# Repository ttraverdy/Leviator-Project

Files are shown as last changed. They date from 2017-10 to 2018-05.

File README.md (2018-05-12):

# What is the Leviator ?

The Leviator is a device made of two arrays of ultrasonic transducers, able to levitate and to control the movements of small objects such as styrofoam beads in 3 dimensions mid-air, using acoustic levitation. 

The levitation is possible thanks to standing wave created by the transducers of the device. Levitating objects are trapped in pressure nodes of those standing waves, surrounded by antinodes, which are going to apply forces on the object, making it levitate. The movements are made by modulating the phase of emission of the transducers. 

This project was awarded a first prize at the XXVth Olypimpiades de Physique, a national physics contest in France.

## How it works

The levitation is possible thanks to standing wave created by the transducers of the device. Levitating objects are trapped in pressure nodes of those standing waves, surrounded by antinodes, which are going to apply forces on the object, making it levitate. The movements are made by modulating the phase of emission of the transducers. 

To see our device work and to have a more precise explication of the movement method, click on the following image to watch a video of our Youtube channel :
<p align="center">
<a href="http://www.youtube.com/watch?feature=player_embedded&v=FV5mTikOukU
" target="_blank">The Leviator, levitation and control of movements using ultrsound</a>
</p>

## Want to build a Leviator ?

The 3D parts are available on this page in the STL folder. Many electronic parts are also necessary (list to be provided soon).

Assemble all the parts (Full instructions should soon be available on Instructables). The Fritzing schematic is available in the SCHEMA folder. It will show you the electronic schematic of the Leviator device.

Run the python 'generateMegaCode16x16new.py' program. This will generate a 'moveArray16x16.io' file in the 'generated' folder. Compile using your Arduino IDE and flash on the Arduino MEGA card.

## Future improvements

<p align="center">
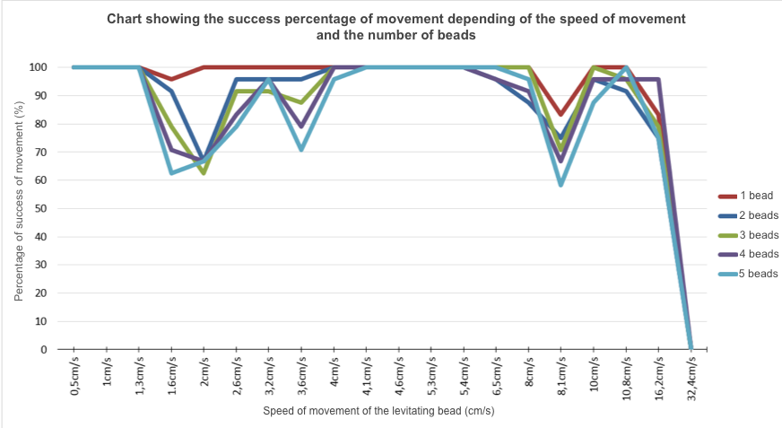
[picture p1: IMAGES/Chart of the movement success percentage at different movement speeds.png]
   
</p>
The actual maximum reliable movement speed is 10.5cm per second for 1 to 5 beads. 100% success rate movement speeds are 0.5cm to 1.5cm/s speeds and speeds from 4.1 to 5.4 cm per second. If more beads are put in a node, the success rate decreases.

We are planning to make a new Leviator, smaller and modular. 3D pieces of the protoype are available in the STL folder. Here is a photo of the actual prototype of the new Leviator. 
<p align="center">
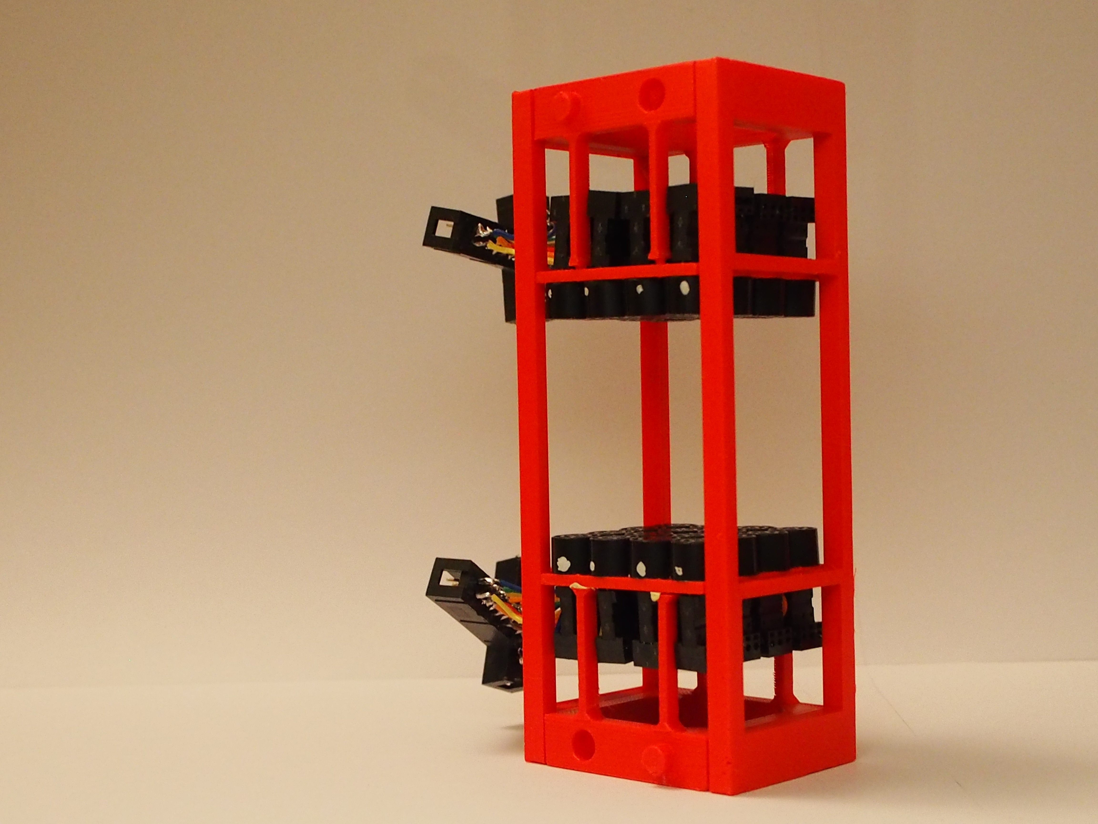
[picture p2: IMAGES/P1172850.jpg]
  
<p align="center">

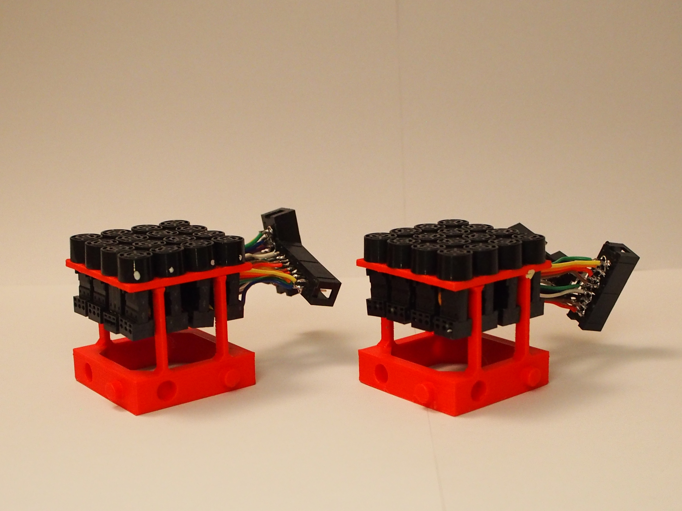
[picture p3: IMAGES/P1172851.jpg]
   
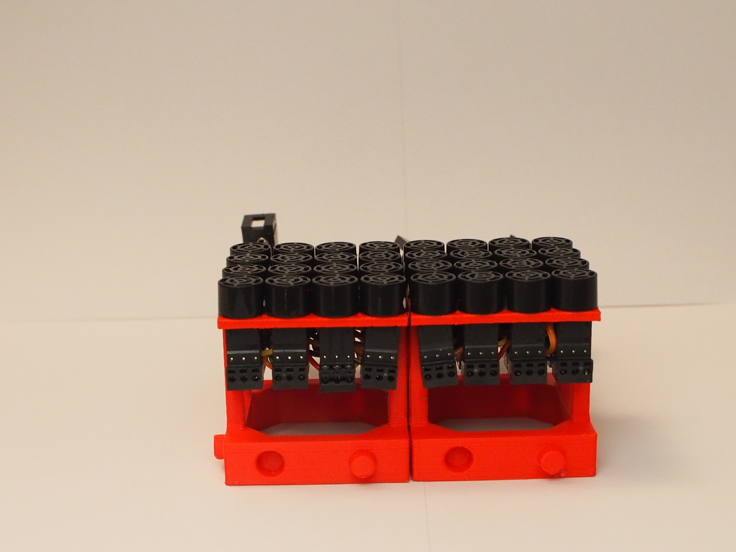
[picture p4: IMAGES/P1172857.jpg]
   
</p>
The new version will be smaller using 10mm diameter transducers and will be modular. Multiple Leviators will be able to be chained to increase the space in which beads will be able to be moved into.

We successfully made a first prototype of the transducer part of the Leviator. We are now working on the miniaturization of power supply of the device. We are actually testing different prototypes such as L293D or TC4427A MOSFET. 
We made different PCB circuits using CNC milling machines or by chemical way using iron perchloride.

## Credits and similar projects

Many thanks to Professor [Takayuki Hoshi](http://hoshistar81.jp/) from the University of Tokyo [Pixie Dust Technologies](http://pixiedusttech.com/) and to Mr. [Asier Marzo](https://www.researchgate.net/profile/Asier_Marzo) from the Bristol University [BigLev/TinyLev and Acoustic Tractor Beam projects](http://www.instructables.com/member/Asier%20Marzo/)

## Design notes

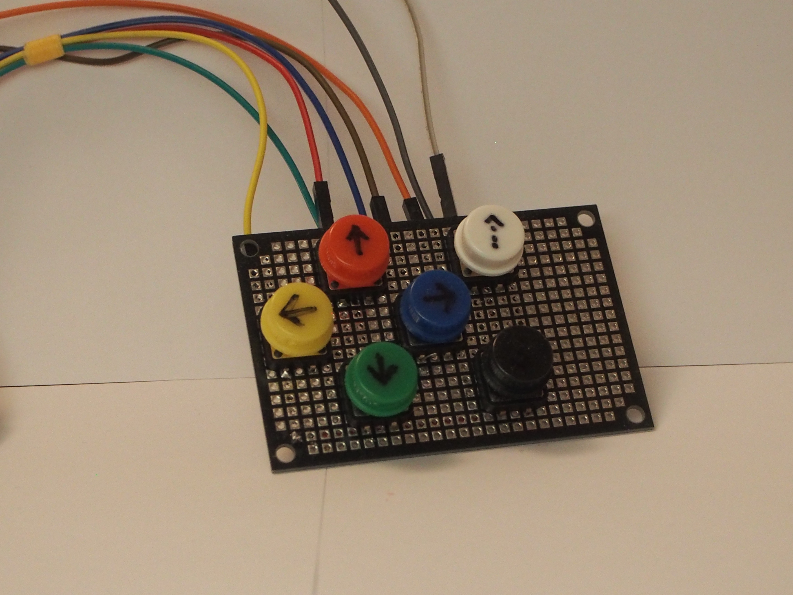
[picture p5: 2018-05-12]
IMAGES/The Leviator button pad.jpg

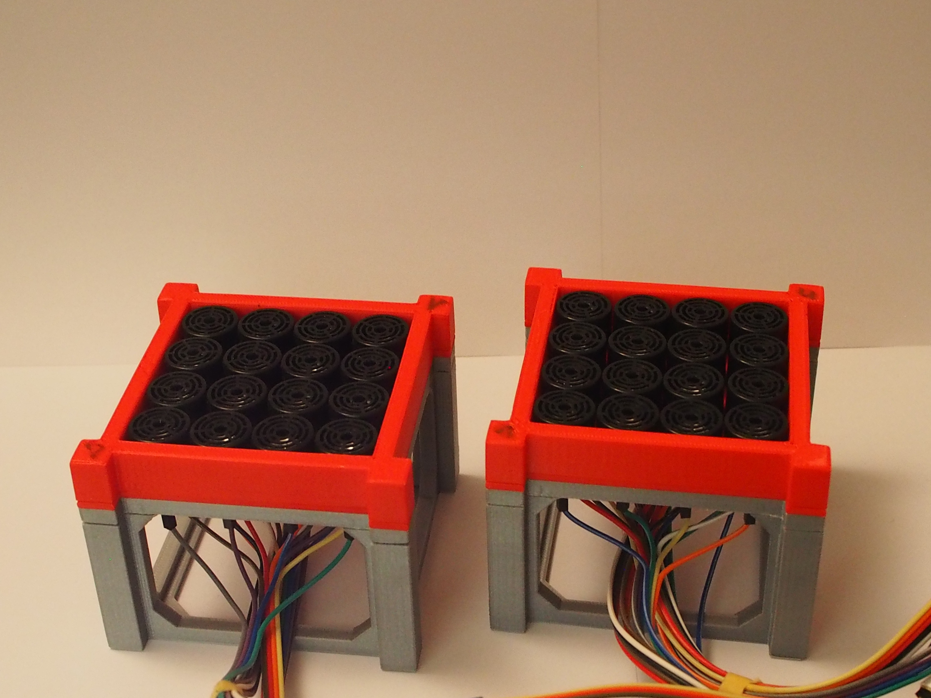
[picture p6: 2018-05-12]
IMAGES/The arrays of the Leviator (1).jpg

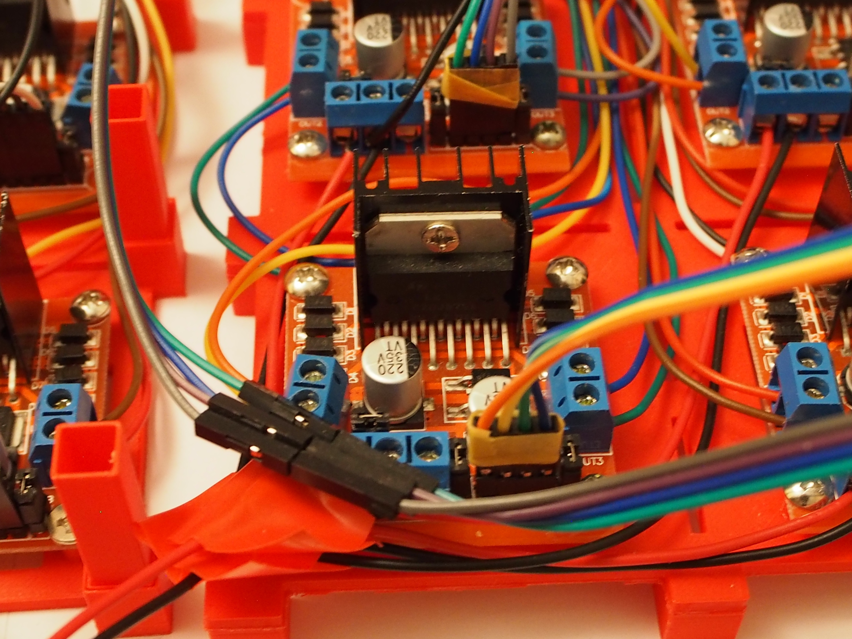
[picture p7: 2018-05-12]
IMAGES/L298N driver block (2).jpg

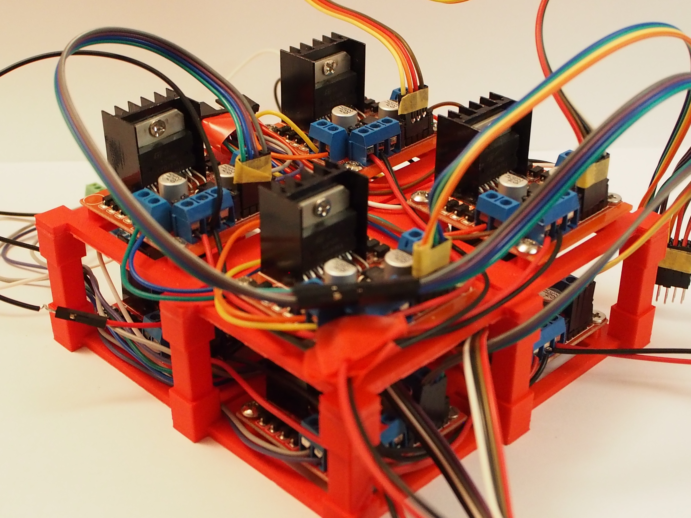
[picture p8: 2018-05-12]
IMAGES/L298N driver block (3).jpg

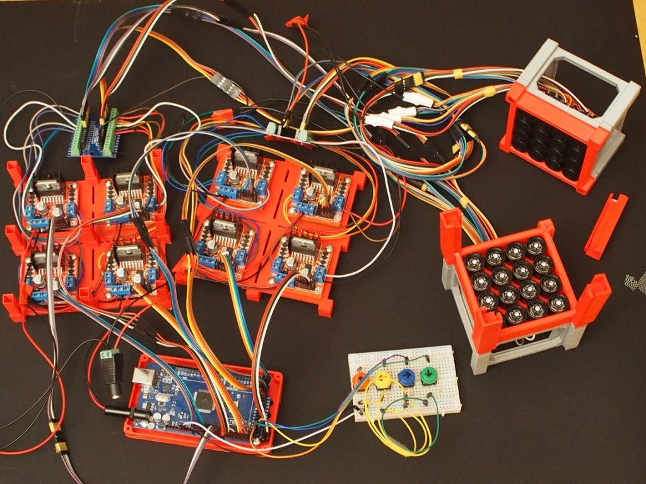
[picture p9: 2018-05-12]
IMAGES/The whole circuit.jpg

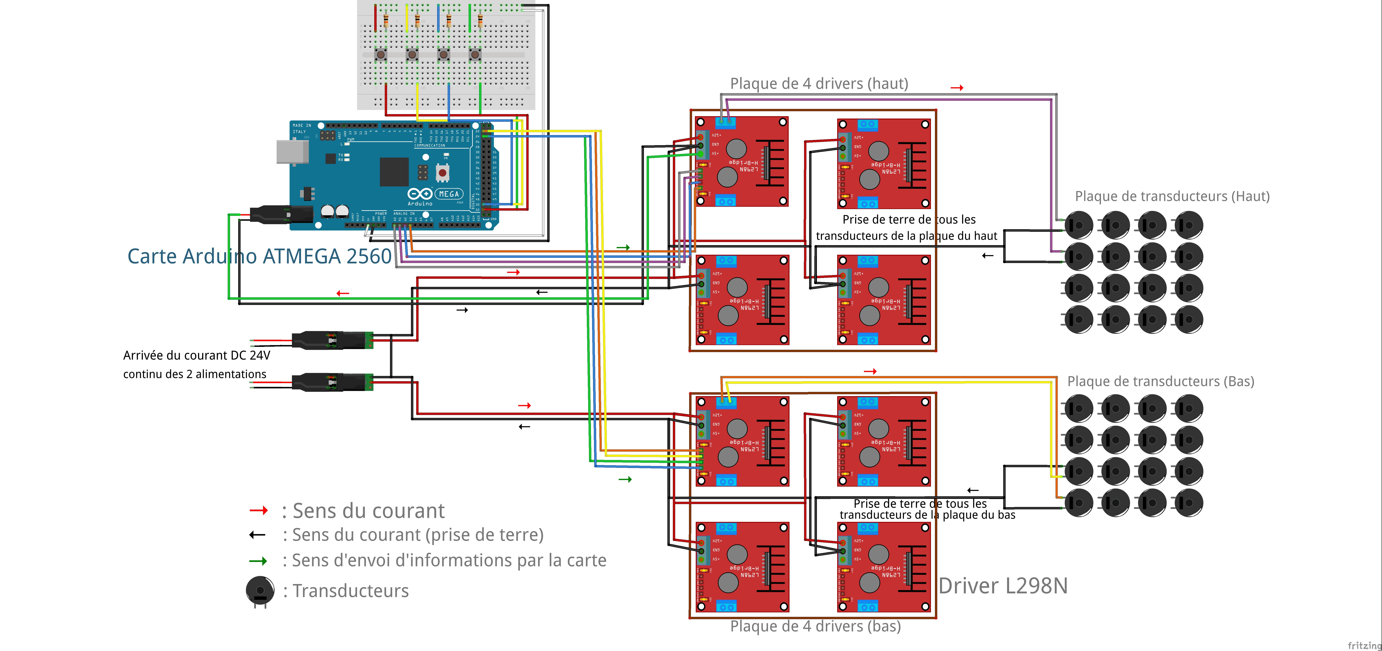
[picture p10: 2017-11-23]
SCHEMA/Schéma Léviator_bb.jpg

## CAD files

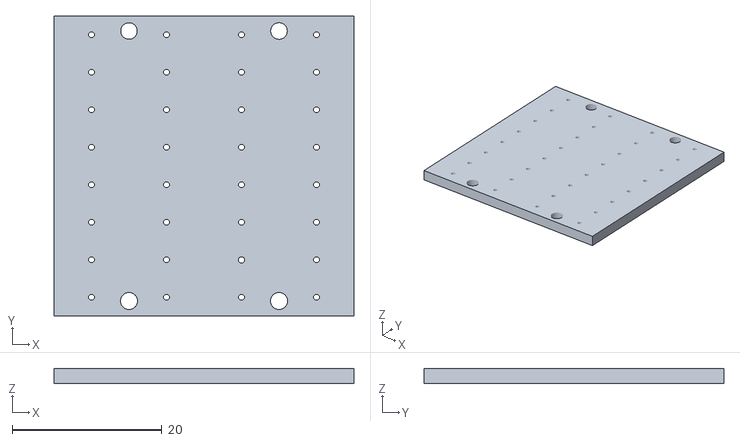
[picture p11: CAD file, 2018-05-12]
STL/Leviator 2 prototype part 2.stl
40.0 x 40.0 x 2.00

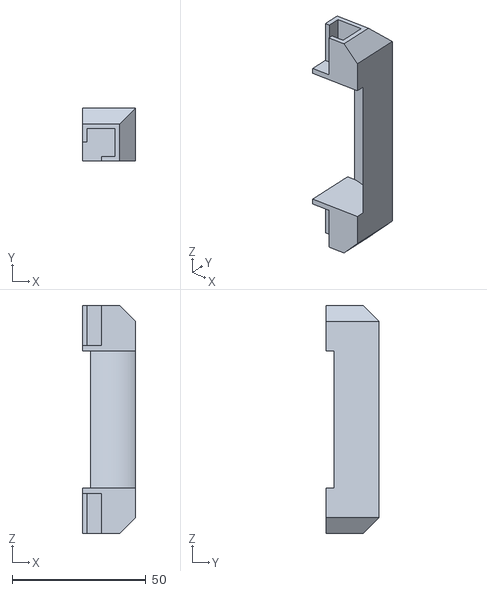
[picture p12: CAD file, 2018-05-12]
STL/Pilar of the Leviator n°3.stl
20.0 x 20.0 x 85.2

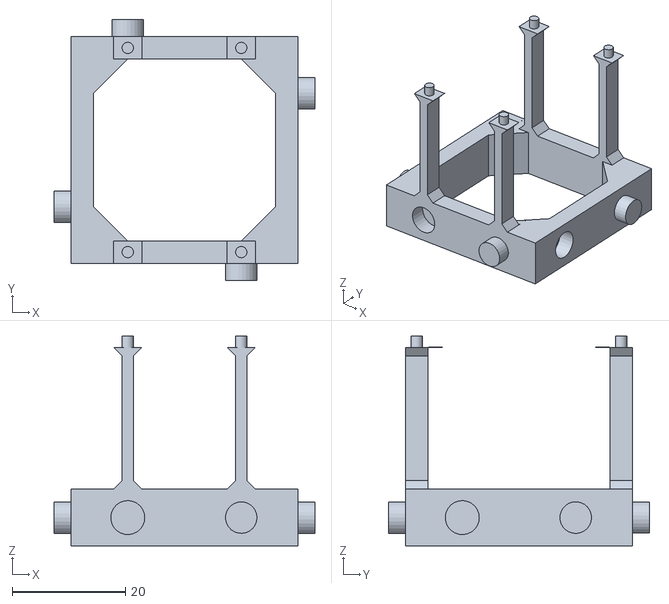
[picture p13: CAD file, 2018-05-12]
STL/Leviator 2 Prototype part 1.stl
46.0 x 46.0 x 37.0

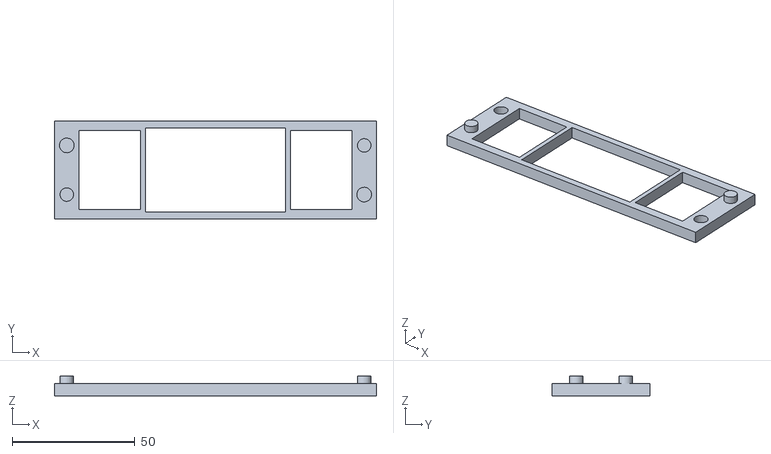
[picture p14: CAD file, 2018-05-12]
STL/Leviator prototype part 3.stl
131.0 x 40.0 x 8.00

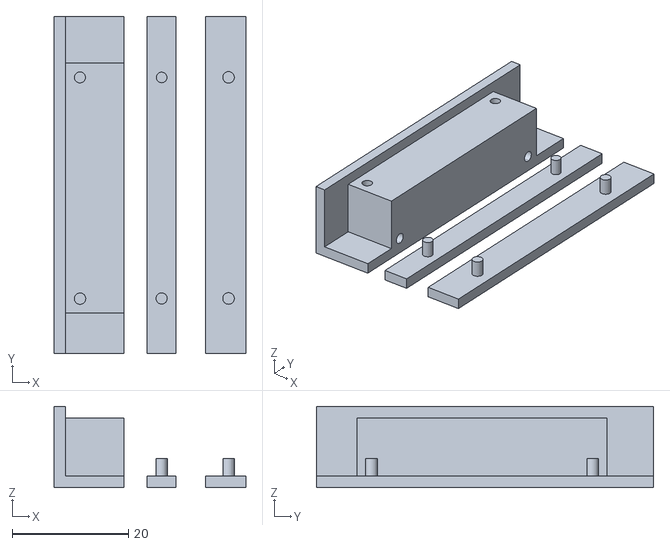
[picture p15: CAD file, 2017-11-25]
STL/Pilar of the Leviator n°2.stl
33.0 x 58.0 x 14.0

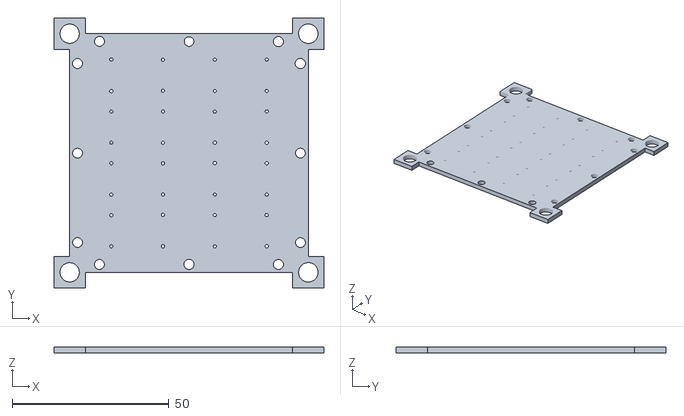
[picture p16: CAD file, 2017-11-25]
STL/Part 3 of the Leviator.stl
86.0 x 86.0 x 2.00

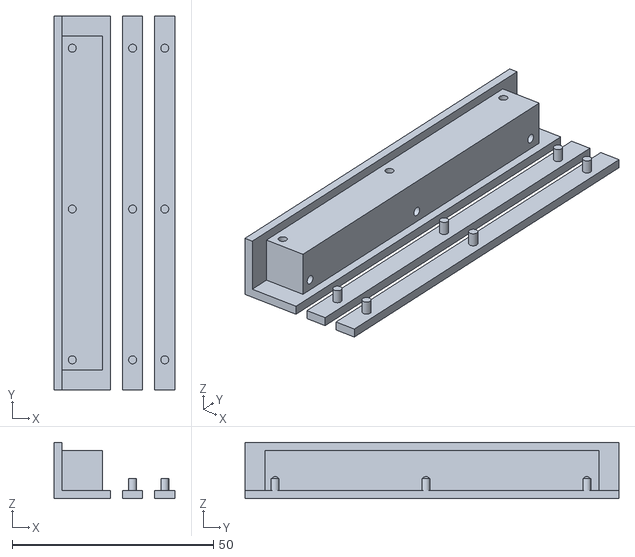
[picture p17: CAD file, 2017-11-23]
STL/Pilar of the Leviator n°1.stl
30.0 x 93.0 x 14.0

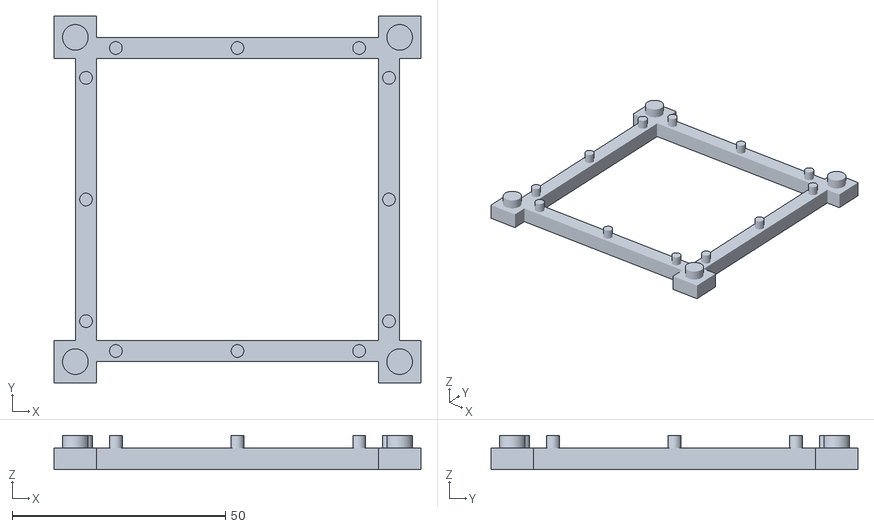
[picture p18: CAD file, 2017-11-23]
STL/Part 2 of the Leviator.stl
86.0 x 86.0 x 8.00

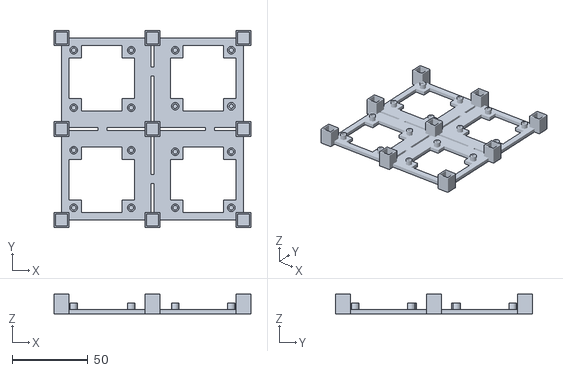
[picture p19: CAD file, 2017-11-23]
STL/Support for L298N drivers bottom.stl
130.0 x 130.0 x 13.0

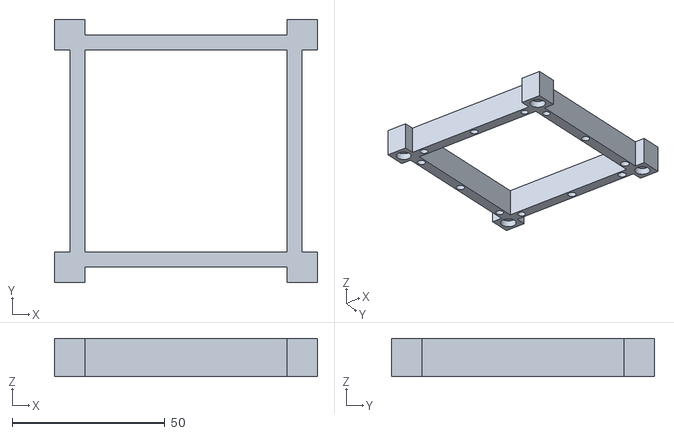
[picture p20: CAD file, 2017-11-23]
STL/Part 4 of the Leviator.stl
86.0 x 86.0 x 12.5

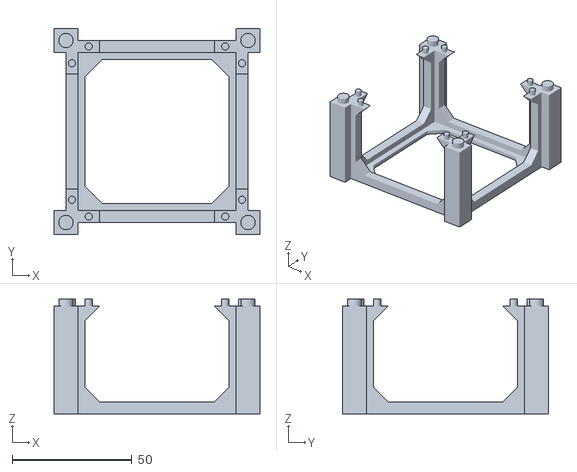
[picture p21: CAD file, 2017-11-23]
STL/Part 1 of the Leviator.stl
86.0 x 86.0 x 48.0

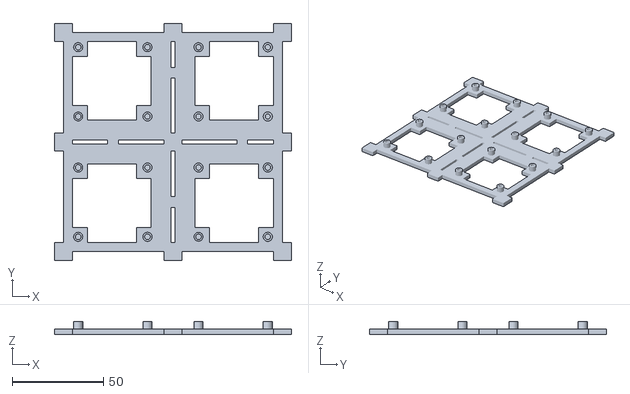
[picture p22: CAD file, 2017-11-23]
STL/Support for 4 L298N drivers top.stl
130.0 x 130.0 x 7.00

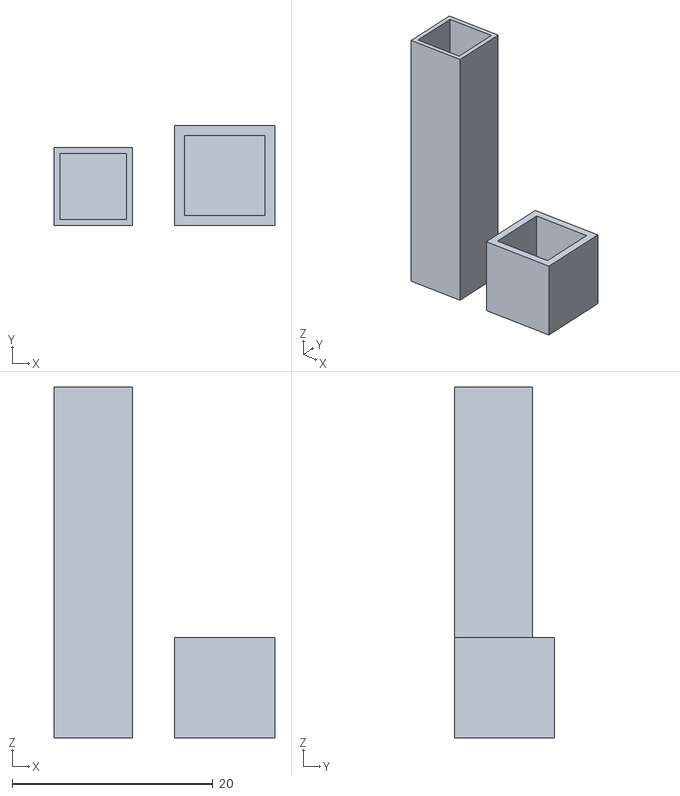
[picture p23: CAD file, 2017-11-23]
STL/Pilar for the support of L298N drivers.stl
22.0 x 10.0 x 35.0

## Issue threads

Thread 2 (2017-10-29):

add button support

ttraverdy, 2017-10-29:
- [x] button input
- [x] test on off

pgraverdy, 2017-11-02:
- cannot use digitalread, too slow for 40khz
- cannot use input_pullup (internal resistor too weak) too many false positive
- with 10komh resistor still some false positive
- added buttonreleased bool to wait for button release before doing the anim again (issue with some false positive from time to time)

Closed 2017-11-02.

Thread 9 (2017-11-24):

Documentation

pgraverdy, 2017-11-24:
- [ ] mettre a jour les noms des fichiers STL (en)
- [ ] mettre le fichier fritzing
- [ ] mettre a jour le readme avec images, ligne de commande
- [ ] mettre a jour le no du prg python, effacer les anciens plus utilisés
- [ ] commenter le code
- [ ] commenter la sortie arduino dans le doc
- [ ] mettre photos du montage complet monté et demonté
- [ ] mettre liste des composants et liens vers sites marchands
- [ ] mettre schema / table de connexion pour les cables sur l'arduino

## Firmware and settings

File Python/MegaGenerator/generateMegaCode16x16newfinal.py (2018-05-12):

#
# This code defines
#
#
#


# defines constants for generating the code for 2 4x4 transducer arrays

# defines the mapping between the port used on the arduino mega and the transducer
# each transducer is indentified with the triplet (s, x, y) with s being the side, and x, y being the position on the array
# two transducers on opposing arrays and with the same x,y are facing each other.
# side can be 0 or 1 (we consider only 2 opposiing array
sides = 2
sizeArray = 4

# number of ports used
nbPortsUsed = 32

# defines the number of frames/steps for each loop.
# this depends of the number of ports used and the time it takes to iterate, still maintiaining the 40Khz freq
# for the initial code (arduino uno, 4 ports it is 24 frames but for many ports, 12 frames should be used
#
MAX_FRAMES = 12
MAX_PORTS = 4

transducersPorts = ['PORTF', 'PORTF', 'PORTF', 'PORTF', 'PORTF', 'PORTF', 'PORTF', 'PORTF',
                    'PORTK', 'PORTK', 'PORTK', 'PORTK', 'PORTK', 'PORTK', 'PORTK', 'PORTK',
                    'PORTA', 'PORTA', 'PORTA', 'PORTA', 'PORTA', 'PORTA', 'PORTA', 'PORTA',
                    'PORTC', 'PORTC', 'PORTC', 'PORTC', 'PORTC', 'PORTC', 'PORTC', 'PORTC']

transducersBitmask = ['00000001', '00000010', '00000100', '00001000', '00010000', '00100000', '01000000', '10000000',
                      '00000001', '00000010', '00000100', '00001000', '00010000', '00100000', '01000000', '10000000',
                      '00000001', '00000010', '00000100', '00001000', '00010000', '00100000', '01000000', '10000000',
                      '10000000', '01000000', '00100000', '00010000', '00001000', '00000100', '00000010', '00000001']

arduinoPorts = ['PORTF', 'PORTK', 'PORTA', 'PORTC']
arduinoPortValues = {}

# we consider that transducers can be at the following state
# 0 - off
# 1 - is the transducer that has the particle
# 2 - is a transducer around the one that has the particule
STATE_TRANSDUCER_OFF = 0
STATE_TRANSDUCER_NB = 1
STATE_TRANSDUCER_PART = 2

transducerFramesOff = [0x00, 0x00, 0x00, 0x00, 0x00, 0x00, 0x00, 0x00, 0x00, 0x00, 0x00, 0x00]
transducerFramesNeighbor2 = [0xff, 0xff, 0xff, 0xff, 0xff, 0xff, 0x00, 0x00, 0x00, 0x00, 0x00, 0x00]
transducerFramesNeighbor3 = [0x00, 0x00, 0x00, 0x00, 0x00, 0x00, 0x00, 0x00, 0x00, 0x00, 0x00, 0x00]
transducerFramesParticle = [0x00, 0x00, 0x00, 0x00, 0x00, 0x00, 0xff, 0xff, 0xff, 0xff, 0xff, 0xff]
transducerFramesNeighbor = [0x00, 0x00, 0x00, 0x00, 0x00, 0x00, 0x00, 0x00, 0x00, 0x00, 0x00, 0x00]

MAX_ANIM_STEPS = 12

STATE_TRANSDUCER_NB2NB = 1
STATE_TRANSDUCER_NB2OFF = 2
STATE_TRANSDUCER_OFF2NB = 3
STATE_TRANSDUCER_OFF2OFF = 4
STATE_TRANSDUCER_NB2PART = 5
STATE_TRANSDUCER_PART2NB = 6
STATE_TRANSDUCER_PART2PART = 7

##
## definitions for animations - various combinations - one is selected after
##

##
## for 10mm transducers
##
# The next tables defines in hexadecimal the action of each postion in object's movement for a Leviator using 10mm transducers

transducerAnimationParticleToParticle10mm = [
# This one defines the evolution of the phase of the 2 transduceurs of the middle of the 6 transducers used in one move
#    [0x00, 0x00, 0x00, 0x00, 0x00, 0x00, 0xff, 0xff, 0xff, 0xff, 0xff, 0xff],
    [0x00, 0x00, 0x00, 0x00, 0x00, 0x00, 0xff, 0xff, 0xff, 0xff, 0xff, 0xff],
    [0x00, 0x00, 0x00, 0x00, 0x00, 0x00, 0xff, 0xff, 0xff, 0xff, 0xff, 0xff],
    [0x00, 0x00, 0x00, 0x00, 0x00, 0xff, 0xff, 0xff, 0xff, 0xff, 0xff, 0x00],
    [0x00, 0x00, 0x00, 0x00, 0x00, 0xff, 0xff, 0xff, 0xff, 0xff, 0xff, 0x00],
    [0x00, 0x00, 0x00, 0x00, 0x00, 0xff, 0xff, 0xff, 0xff, 0xff, 0xff, 0x00],
    [0x00, 0x00, 0x00, 0x00, 0x00, 0xff, 0xff, 0xff, 0xff, 0xff, 0xff, 0x00],
    [0x00, 0x00, 0x00, 0x00, 0x00, 0xff, 0xff, 0xff, 0xff, 0xff, 0xff, 0x00],
    [0x00, 0x00, 0x00, 0x00, 0x00, 0xff, 0xff, 0xff, 0xff, 0xff, 0xff, 0x00],
    [0x00, 0x00, 0x00, 0x00, 0x00, 0xff, 0xff, 0xff, 0xff, 0xff, 0xff, 0x00],
    [0x00, 0x00, 0x00, 0x00, 0x00, 0x00, 0xff, 0xff, 0xff, 0xff, 0xff, 0xff],
    [0x00, 0x00, 0x00, 0x00, 0x00, 0x00, 0xff, 0xff, 0xff, 0xff, 0xff, 0xff],
    [0x00, 0x00, 0x00, 0x00, 0x00, 0x00, 0xff, 0xff, 0xff, 0xff, 0xff, 0xff]
]


transducerAnimationParticleToNeighbor10mm = [
# This one defines the evolution of the phase of the 2 transduceurs of the old postion of the 6 transducers used in one move

#    [0xff, 0xff, 0xff, 0xff, 0xff, 0x00, 0x00, 0x00, 0x00, 0x00, 0x00, 0xff]
    [0xff, 0xff, 0xff, 0xff, 0xff, 0x00, 0x00, 0x00, 0x00, 0x00, 0x00, 0xff],
    [0xff, 0xff, 0xff, 0xff, 0x00, 0x00, 0x00, 0x00, 0x00, 0x00, 0xff, 0xff],
    [0xff, 0xff, 0xff, 0x00, 0x00, 0x00, 0x00, 0x00, 0x00, 0xff, 0xff, 0xff],
    [0xff, 0xff, 0xff, 0x00, 0x00, 0x00, 0x00, 0x00, 0x00, 0xff, 0xff, 0xff],
    [0xff, 0xff, 0x00, 0x00, 0x00, 0x00, 0x00, 0x00, 0xff, 0xff, 0xff, 0xff],
    [0xff, 0xff, 0x00, 0x00, 0x00, 0x00, 0x00, 0x00, 0xff, 0xff, 0xff, 0xff],
    [0xff, 0xff, 0x00, 0x00, 0x00, 0x00, 0x00, 0x00, 0xff, 0xff, 0xff, 0xff],
    [0xff, 0x00, 0x00, 0x00, 0x00, 0x00, 0x00, 0xff, 0xff, 0xff, 0xff, 0xff],
    [0xff, 0x00, 0x00, 0x00, 0x00, 0x00, 0x00, 0xff, 0xff, 0xff, 0xff, 0xff],
    [0xff, 0x00, 0x00, 0x00, 0x00, 0x00, 0x00, 0xff, 0xff, 0xff, 0xff, 0xff],
    [0x00, 0x00, 0x00, 0x00, 0x00, 0x00, 0xff, 0xff, 0xff, 0xff, 0xff, 0xff],
    [0x00, 0x00, 0x00, 0x00, 0x00, 0x00, 0xff, 0xff, 0xff, 0xff, 0xff, 0xff]
]

transducerAnimationNeighborToParticle10mm = [
# This one defines the evolution of the phase of the 2 transduceurs of the new postion of the 6 transducers used in one move

#    [0x00, 0x00, 0x00, 0x00, 0x00, 0x00, 0xff, 0xff, 0xff, 0xff, 0xff, 0xff]
    [0x00, 0x00, 0x00, 0x00, 0x00, 0x00, 0xff, 0xff, 0xff, 0xff, 0xff, 0xff],
    [0xff, 0x00, 0x00, 0x00, 0x00, 0x00, 0x00, 0xff, 0xff, 0xff, 0xff, 0xff],
    [0xff, 0x00, 0x00, 0x00, 0x00, 0x00, 0x00, 0xff, 0xff, 0xff, 0xff, 0xff],
    [0xff, 0x00, 0x00, 0x00, 0x00, 0x00, 0x00, 0xff, 0xff, 0xff, 0xff, 0xff],
    [0xff, 0xff, 0x00, 0x00, 0x00, 0x00, 0x00, 0x00, 0xff, 0xff, 0xff, 0xff],
    [0xff, 0xff, 0x00, 0x00, 0x00, 0x00, 0x00, 0x00, 0xff, 0xff, 0xff, 0xff],
    [0xff, 0xff, 0x00, 0x00, 0x00, 0x00, 0x00, 0x00, 0xff, 0xff, 0xff, 0xff],
    [0xff, 0xff, 0xff, 0x00, 0x00, 0x00, 0x00, 0x00, 0x00, 0xff, 0xff, 0xff],
    [0xff, 0xff, 0xff, 0x00, 0x00, 0x00, 0x00, 0x00, 0x00, 0xff, 0xff, 0xff],
    [0xff, 0xff, 0xff, 0xff, 0x00, 0x00, 0x00, 0x00, 0x00, 0x00, 0xff, 0xff],
    [0xff, 0xff, 0xff, 0xff, 0xff, 0x00, 0x00, 0x00, 0x00, 0x00, 0x00, 0xff],
    [0xff, 0xff, 0xff, 0xff, 0xff, 0x00, 0x00, 0x00, 0x00, 0x00, 0x00, 0xff]
]

## 16mm - phase 32mm

transducerAnimationParticleToParticle16mm = [
# This one defines the evolution of the phase of the 2 transduceurs of the middle of the 6 transducers used in one move

    [0x00, 0x00, 0x00, 0x00, 0x00, 0x00, 0xff, 0xff, 0xff, 0xff, 0xff, 0xff],
    [0x00, 0x00, 0x00, 0x00, 0x00, 0x00, 0xff, 0xff, 0xff, 0xff, 0xff, 0xff],
    [0x00, 0x00, 0x00, 0x00, 0x00, 0xff, 0xff, 0xff, 0xff, 0xff, 0xff, 0x00],
    [0x00, 0x00, 0x00, 0x00, 0x00, 0xff, 0xff, 0xff, 0xff, 0xff, 0xff, 0x00],
    [0x00, 0x00, 0x00, 0x00, 0x00, 0xff, 0xff, 0xff, 0xff, 0xff, 0xff, 0x00],
    [0x00, 0x00, 0x00, 0x00, 0x00, 0xff, 0xff, 0xff, 0xff, 0xff, 0xff, 0x00],
#    [0x00, 0x00, 0x00, 0x00, 0x00, 0xff, 0xff, 0xff, 0xff, 0xff, 0xff, 0x00],
    [0x00, 0x00, 0x00, 0x00, 0x00, 0xff, 0xff, 0xff, 0xff, 0xff, 0xff, 0x00],
    [0x00, 0x00, 0x00, 0x00, 0x00, 0xff, 0xff, 0xff, 0xff, 0xff, 0xff, 0x00],
    [0x00, 0x00, 0x00, 0x00, 0x00, 0xff, 0xff, 0xff, 0xff, 0xff, 0xff, 0x00],
    [0x00, 0x00, 0x00, 0x00, 0x00, 0xff, 0xff, 0xff, 0xff, 0xff, 0xff, 0x00],
    [0x00, 0x00, 0x00, 0x00, 0x00, 0x00, 0xff, 0xff, 0xff, 0xff, 0xff, 0xff],
    [0x00, 0x00, 0x00, 0x00, 0x00, 0x00, 0xff, 0xff, 0xff, 0xff, 0xff, 0xff]
]

transducerAnimationParticleToNeighbor16mm = [
# This one defines the evolution of the phase of the 2 transduceurs of the old postion of the 6 transducers used in one move

    [0x00, 0x00, 0x00, 0x00, 0xff, 0xff, 0xff, 0xff, 0xff, 0xff, 0x00, 0x00],
    [0x00, 0x00, 0x00, 0xff, 0xff, 0xff, 0xff, 0xff, 0xff, 0x00, 0x00, 0x00],
    [0x00, 0x00, 0xff, 0xff, 0xff, 0xff, 0xff, 0xff, 0x00, 0x00, 0x00, 0x00],
    [0x00, 0xff, 0xff, 0xff, 0xff, 0xff, 0xff, 0x00, 0x00, 0x00, 0x00, 0x00],
    [0xff, 0xff, 0xff, 0xff, 0xff, 0xff, 0x00, 0x00, 0x00, 0x00, 0x00, 0x00],
    [0xff, 0xff, 0xff, 0xff, 0xff, 0x00, 0x00, 0x00, 0x00, 0x00, 0x00, 0xff],
#    [0xff, 0xff, 0xff, 0xff, 0x00, 0x00, 0x00, 0x00, 0x00, 0x00, 0xff, 0xff],
    [0xff, 0xff, 0xff, 0x00, 0x00, 0x00, 0x00, 0x00, 0x00, 0xff, 0xff, 0xff],
    [0xff, 0xff, 0x00, 0x00, 0x00, 0x00, 0x00, 0x00, 0xff, 0xff, 0xff, 0xff],
    [0xff, 0xff, 0x00, 0x00, 0x00, 0x00, 0x00, 0x00, 0xff, 0xff, 0xff, 0xff],
    [0xff, 0x00, 0x00, 0x00, 0x00, 0x00, 0x00, 0xff, 0xff, 0xff, 0xff, 0xff],
    [0xff, 0x00, 0x00, 0x00, 0x00, 0x00, 0x00, 0xff, 0xff, 0xff, 0xff, 0xff],
    [0x00, 0x00, 0x00, 0x00, 0x00, 0x00, 0xff, 0xff, 0xff, 0xff, 0xff, 0xff]
]
transducerAnimationNeighborToParticle16mm = [
# This one defines the evolution of the phase of the 2 transduceurs of the new postion of the 6 transducers used in one move

    [0x00, 0x00, 0x00, 0x00, 0x00, 0x00, 0xff, 0xff, 0xff, 0xff, 0xff, 0xff],
    [0xff, 0x00, 0x00, 0x00, 0x00, 0x00, 0x00, 0xff, 0xff, 0xff, 0xff, 0xff],
    [0xff, 0x00, 0x00, 0x00, 0x00, 0x00, 0x00, 0xff, 0xff, 0xff, 0xff, 0xff],
    [0xff, 0xff, 0x00, 0x00, 0x00, 0x00, 0x00, 0x00, 0xff, 0xff, 0xff, 0xff],
    [0xff, 0xff, 0x00, 0x00, 0x00, 0x00, 0x00, 0x00, 0xff, 0xff, 0xff, 0xff],
    [0xff, 0xff, 0xff, 0x00, 0x00, 0x00, 0x00, 0x00, 0x00, 0xff, 0xff, 0xff],
#    [0xff, 0xff, 0xff, 0xff, 0x00, 0x00, 0x00, 0x00, 0x00, 0x00, 0xff, 0xff],
    [0xff, 0xff, 0xff, 0xff, 0xff, 0x00, 0x00, 0x00, 0x00, 0x00, 0x00, 0xff],
    [0xff, 0xff, 0xff, 0xff, 0xff, 0xff, 0x00, 0x00, 0x00, 0x00, 0x00, 0x00],
    [0x00, 0xff, 0xff, 0xff, 0xff, 0xff, 0xff, 0x00, 0x00, 0x00, 0x00, 0x00],
    [0x00, 0x00, 0xff, 0xff, 0xff, 0xff, 0xff, 0xff, 0x00, 0x00, 0x00, 0x00],
    [0x00, 0x00, 0x00, 0xff, 0xff, 0xff, 0xff, 0xff, 0xff, 0x00, 0x00, 0x00],
    [0x00, 0x00, 0x00, 0x00, 0xff, 0xff, 0xff, 0xff, 0xff, 0xff, 0x00, 0x00]
]


##
## Amplitude
##

#different tables of hexadecimal values for transducers activation for movement using the amplitude modulation method, which isn't very trustworthy

transducerAnimationParticleToNeighborGOOD = [
    [0x00, 0x00, 0x00, 0x00, 0x00, 0x00, 0x00, 0x00, 0xff, 0xff, 0x00, 0x00],
    [0x00, 0x00, 0x00, 0x00, 0x00, 0x00, 0x00, 0x00, 0x00, 0xff, 0x00, 0x00],
    [0x00, 0x00, 0x00, 0x00, 0x00, 0x00, 0x00, 0x00, 0x00, 0xff, 0x00, 0x00],
    [0x00, 0x00, 0x00, 0x00, 0x00, 0x00, 0x00, 0x00, 0x00, 0x00, 0x00, 0x00],
    [0x00, 0x00, 0x00, 0x00, 0x00, 0x00, 0x00, 0x00, 0x00, 0x00, 0x00, 0x00],
    [0x00, 0x00, 0xff, 0x00, 0x00, 0x00, 0x00, 0x00, 0x00, 0x00, 0x00, 0x00],
    [0x00, 0x00, 0xff, 0x00, 0x00, 0x00, 0x00, 0x00, 0x00, 0x00, 0x00, 0x00],
    [0x00, 0xff, 0xff, 0xff, 0x00, 0x00, 0x00, 0x00, 0x00, 0x00, 0x00, 0x00],
    [0x00, 0x00, 0xff, 0x00, 0x00, 0x00, 0x00, 0x00, 0x00, 0x00, 0x00, 0x00],
    [0x00, 0x00, 0xff, 0x00, 0x00, 0x00, 0x00, 0x00, 0x00, 0x00, 0x00, 0x00],
    [0x00, 0x00, 0x00, 0x00, 0x00, 0x00, 0x00, 0x00, 0x00, 0x00, 0x00, 0x00],
    [0x00, 0x00, 0x00, 0x00, 0x00, 0x00, 0x00, 0x00, 0x00, 0x00, 0x00, 0x00],
    [0x00, 0x00, 0x00, 0x00, 0x00, 0x00, 0x00, 0x00, 0x00, 0x00, 0x00, 0x00],
    [0x00, 0x00, 0x00, 0x00, 0x00, 0x00, 0x00, 0x00, 0x00, 0x00, 0x00, 0x00],
    [0x00, 0x00, 0x00, 0x00, 0x00, 0x00, 0x00, 0x00, 0x00, 0x00, 0x00, 0x00],
    [0x00, 0x00, 0x00, 0x00, 0x00, 0x00, 0x00, 0x00, 0x00, 0x00, 0x00, 0x00]
]

transducerAnimationParticleToParticleGOOD = [
    [0x00, 0x00, 0x00, 0x00, 0x00, 0x00, 0xff, 0xff, 0xff, 0xff, 0xff, 0xff],
    [0x00, 0x00, 0x00, 0x00, 0x00, 0x00, 0xff, 0xff, 0xff, 0xff, 0xff, 0xff],
    [0x00, 0x00, 0x00, 0x00, 0x00, 0x00, 0xff, 0xff, 0xff, 0xff, 0xff, 0xff],
    [0x00, 0x00, 0x00, 0x00, 0x00, 0x00, 0xff, 0xff, 0xff, 0xff, 0xff, 0xff],
    [0x00, 0x00, 0x00, 0x00, 0x00, 0x00, 0xff, 0xff, 0xff, 0xff, 0xff, 0xff],
    [0x00, 0x00, 0x00, 0x00, 0x00, 0x00, 0xff, 0xff, 0xff, 0xff, 0xff, 0xff],
    [0x00, 0x00, 0x00, 0x00, 0x00, 0x00, 0x00, 0xff, 0xff, 0xff, 0xff, 0x00],
    [0x00, 0x00, 0x00, 0x00, 0x00, 0x00, 0x00, 0xff, 0xff, 0xff, 0xff, 0x00],
    [0x00, 0x00, 0x00, 0x00, 0x00, 0x00, 0x00, 0x00, 0xff, 0xff, 0x00, 0x00],
    [0x00, 0x00, 0x00, 0x00, 0x00, 0x00, 0x00, 0x00, 0xff, 0xff, 0x00, 0x00],
    [0x00, 0x00, 0x00, 0x00, 0x00, 0x00, 0x00, 0x00, 0x00, 0xff, 0x00, 0x00],
    [0x00, 0x00, 0x00, 0x00, 0x00, 0x00, 0x00, 0x00, 0xff, 0xff, 0x00, 0x00],
    [0x00, 0x00, 0x00, 0x00, 0x00, 0x00, 0x00, 0xff, 0xff, 0xff, 0xff, 0x00],
    [0x00, 0x00, 0x00, 0x00, 0x00, 0x00, 0x00, 0xff, 0xff, 0xff, 0xff, 0x00],
    [0x00, 0x00, 0x00, 0x00, 0x00, 0x00, 0xff, 0xff, 0xff, 0xff, 0xff, 0xff],
    [0x00, 0x00, 0x00, 0x00, 0x00, 0x00, 0xff, 0xff, 0xff, 0xff, 0xff, 0xff]
]

# better than transducerAnimationNeighborToParticle4
transducerAnimationNeighborToParticleGOOD = [
    [0x00, 0x00, 0x00, 0x00, 0x00, 0x00, 0x00, 0x00, 0x00, 0x00, 0x00, 0x00],
    [0x00, 0x00, 0x00, 0x00, 0x00, 0x00, 0x00, 0x00, 0x00, 0x00, 0x00, 0x00],
    [0x00, 0x00, 0x00, 0x00, 0x00, 0x00, 0x00, 0x00, 0x00, 0x00, 0x00, 0x00],
    [0x00, 0x00, 0x00, 0x00, 0x00, 0x00, 0x00, 0x00, 0x00, 0x00, 0x00, 0x00],
    [0x00, 0x00, 0x00, 0x00, 0x00, 0x00, 0x00, 0x00, 0x00, 0x00, 0x00, 0x00],
    [0x00, 0x00, 0x00, 0x00, 0x00, 0x00, 0x00, 0x00, 0x00, 0x00, 0x00, 0x00],
    [0x00, 0x00, 0x00, 0x00, 0x00, 0x00, 0x00, 0x00, 0x00, 0xff, 0x00, 0x00],
    [0x00, 0x00, 0x00, 0x00, 0x00, 0x00, 0x00, 0x00, 0xff, 0xff, 0x00, 0x00],
    [0x00, 0x00, 0x00, 0x00, 0x00, 0x00, 0x00, 0x00, 0xff, 0xff, 0x00, 0x00],
    [0x00, 0x00, 0x00, 0x00, 0x00, 0x00, 0x00, 0xff, 0xff, 0xff, 0x00, 0x00],
    [0x00, 0x00, 0x00, 0x00, 0x00, 0x00, 0x00, 0xff, 0xff, 0xff, 0xff, 0x00],
    [0x00, 0x00, 0x00, 0x00, 0x00, 0x00, 0x00, 0xff, 0xff, 0xff, 0xff, 0x00],
    [0x00, 0x00, 0x00, 0x00, 0x00, 0x00, 0xff, 0xff, 0xff, 0xff, 0xff, 0xff],
    [0x00, 0x00, 0x00, 0x00, 0x00, 0x00, 0xff, 0xff, 0xff, 0xff, 0xff, 0xff],
    [0x00, 0x00, 0x00, 0x00, 0x00, 0x00, 0xff, 0xff, 0xff, 0xff, 0xff, 0xff],
    [0x00, 0x00, 0x00, 0x00, 0x00, 0x00, 0xff, 0xff, 0xff, 0xff, 0xff, 0xff]
]
##
## Misc
##

#
transducerAnimationParticleToNeighbor4 = [
    [0x00, 0x00, 0x00, 0x00, 0x00, 0x00, 0x00, 0x00, 0xff, 0xff, 0x00, 0x00],
    [0x00, 0x00, 0x00, 0x00, 0x00, 0x00, 0x00, 0x00, 0x00, 0xff, 0x00, 0x00],
    [0x00, 0x00, 0x00, 0x00, 0x00, 0x00, 0x00, 0x00, 0x00, 0xff, 0x00, 0x00],
    [0x00, 0x00, 0x00, 0x00, 0x00, 0x00, 0x00, 0x00, 0x00, 0x00, 0x00, 0x00],
    [0x00, 0x00, 0x00, 0x00, 0x00, 0x00, 0x00, 0x00, 0x00, 0x00, 0x00, 0x00],
    [0x00, 0x00, 0xff, 0x00, 0x00, 0x00, 0x00, 0x00, 0x00, 0x00, 0x00, 0x00],
    [0x00, 0x00, 0xff, 0x00, 0x00, 0x00, 0x00, 0x00, 0x00, 0x00, 0x00, 0x00],
    [0x00, 0xff, 0xff, 0xff, 0x00, 0x00, 0x00, 0x00, 0x00, 0x00, 0x00, 0x00],
    [0x00, 0x00, 0xff, 0x00, 0x00, 0x00, 0x00, 0x00, 0x00, 0x00, 0x00, 0x00],
    [0x00, 0x00, 0xff, 0x00, 0x00, 0x00, 0x00, 0x00, 0x00, 0x00, 0x00, 0x00],
    [0x00, 0x00, 0x00, 0x00, 0x00, 0x00, 0x00, 0x00, 0x00, 0x00, 0x00, 0x00],
    [0x00, 0x00, 0x00, 0x00, 0x00, 0x00, 0x00, 0x00, 0x00, 0x00, 0x00, 0x00],
    [0x00, 0x00, 0x00, 0x00, 0x00, 0x00, 0x00, 0x00, 0x00, 0x00, 0x00, 0x00],
    [0x00, 0x00, 0x00, 0x00, 0x00, 0x00, 0x00, 0x00, 0x00, 0x00, 0x00, 0x00],
    [0x00, 0x00, 0x00, 0x00, 0x00, 0x00, 0x00, 0x00, 0x00, 0x00, 0x00, 0x00],
    [0x00, 0x00, 0x00, 0x00, 0x00, 0x00, 0x00, 0x00, 0x00, 0x00, 0x00, 0x00]
]

transducerAnimationParticleToNeighbor3 = [
    [0x00, 0x00, 0x00, 0x00, 0x00, 0x00, 0x00, 0xff, 0xff, 0xff, 0xff, 0x00],
    [0x00, 0x00, 0x00, 0x00, 0x00, 0x00, 0x00, 0xff, 0xff, 0xff, 0xff, 0x00],
    [0x00, 0x00, 0x00, 0x00, 0x00, 0x00, 0x00, 0x00, 0xff, 0xff, 0xff, 0x00],
    [0x00, 0x00, 0x00, 0x00, 0x00, 0x00, 0x00, 0x00, 0xff, 0xff, 0xff, 0x00],
    [0x00, 0x00, 0x00, 0x00, 0x00, 0x00, 0x00, 0x00, 0xff, 0xff, 0x00, 0x00],
    [0x00, 0x00, 0x00, 0x00, 0x00, 0x00, 0x00, 0x00, 0xff, 0xff, 0x00, 0x00],
    [0x00, 0x00, 0x00, 0x00, 0x00, 0x00, 0x00, 0x00, 0xff, 0xff, 0x00, 0x00],
    [0x00, 0x00, 0x00, 0x00, 0x00, 0x00, 0x00, 0x00, 0xff, 0xff, 0x00, 0x00],
    [0x00, 0x00, 0x00, 0xff, 0x00, 0x00, 0x00, 0x00, 0x00, 0x00, 0x00, 0x00],
    [0x00, 0x00, 0xff, 0xff, 0x00, 0x00, 0x00, 0x00, 0x00, 0x00, 0x00, 0x00],
    [0x00, 0x00, 0xff, 0xff, 0x00, 0x00, 0x00, 0x00, 0x00, 0x00, 0x00, 0x00],
    [0x00, 0x00, 0xff, 0xff, 0xff, 0x00, 0x00, 0x00, 0x00, 0x00, 0x00, 0x00],
    [0x00, 0xff, 0xff, 0xff, 0xff, 0x00, 0x00, 0x00, 0x00, 0x00, 0x00, 0x00],
    [0x00, 0xff, 0xff, 0xff, 0xff, 0xff, 0x00, 0x00, 0x00, 0x00, 0x00, 0x00],
    [0x00, 0xff, 0xff, 0xff, 0xff, 0xff, 0x00, 0x00, 0x00, 0x00, 0x00, 0x00],
    [0x00, 0xff, 0xff, 0xff, 0xff, 0xff, 0x00, 0x00, 0x00, 0x00, 0x00, 0x00]
]

transducerAnimationParticleToNeighbor2 = [
    [0x00, 0x00, 0x00, 0x00, 0x00, 0x00, 0xff, 0xff, 0xff, 0xff, 0xff, 0x00],
    [0x00, 0x00, 0x00, 0x00, 0x00, 0x00, 0x00, 0xff, 0xff, 0xff, 0xff, 0x00],
    [0x00, 0x00, 0x00, 0x00, 0x00, 0x00, 0x00, 0xff, 0xff, 0xff, 0xff, 0x00],
    [0x00, 0x00, 0x00, 0x00, 0x00, 0x00, 0x00, 0xff, 0xff, 0xff, 0x00, 0x00],
    [0x00, 0x00, 0x00, 0x00, 0x00, 0x00, 0x00, 0xff, 0xff, 0xff, 0x00, 0x00],
    [0x00, 0x00, 0x00, 0x00, 0x00, 0x00, 0x00, 0x00, 0xff, 0xff, 0x00, 0x00],
    [0x00, 0x00, 0x00, 0x00, 0x00, 0x00, 0x00, 0x00, 0xff, 0xff, 0x00, 0x00],
    [0x00, 0x00, 0x00, 0x00, 0x00, 0x00, 0x00, 0x00, 0x00, 0xff, 0x00, 0x00],
    [0x00, 0x00, 0x00, 0xff, 0x00, 0x00, 0x00, 0x00, 0x00, 0x00, 0x00, 0x00],
    [0x00, 0x00, 0xff, 0xff, 0x00, 0x00, 0x00, 0x00, 0x00, 0x00, 0x00, 0x00],
    [0x00, 0x00, 0xff, 0xff, 0x00, 0x00, 0x00, 0x00, 0x00, 0x00, 0x00, 0x00],
    [0x00, 0x00, 0xff, 0xff, 0xff, 0x00, 0x00, 0x00, 0x00, 0x00, 0x00, 0x00],
    [0x00, 0xff, 0xff, 0xff, 0xff, 0x00, 0x00, 0x00, 0x00, 0x00, 0x00, 0x00],
    [0x00, 0xff, 0xff, 0xff, 0xff, 0xff, 0x00, 0x00, 0x00, 0x00, 0x00, 0x00],
    [0x00, 0xff, 0xff, 0xff, 0xff, 0xff, 0x00, 0x00, 0x00, 0x00, 0x00, 0x00],
    [0x00, 0xff, 0xff, 0xff, 0xff, 0xff, 0x00, 0x00, 0x00, 0x00, 0x00, 0x00]
]


transducerAnimationParticleToParticle3 = [
    [0x00, 0x00, 0x00, 0x00, 0x00, 0x00, 0xff, 0xff, 0xff, 0xff, 0xff, 0xff],
    [0x00, 0x00, 0x00, 0x00, 0x00, 0x00, 0xff, 0xff, 0xff, 0xff, 0xff, 0xff],
    [0x00, 0x00, 0x00, 0x00, 0x00, 0x00, 0xff, 0xff, 0xff, 0xff, 0xff, 0xff],
    [0x00, 0x00, 0x00, 0x00, 0x00, 0x00, 0xff, 0xff, 0xff, 0xff, 0xff, 0xff],
    [0x00, 0x00, 0x00, 0x00, 0x00, 0x00, 0xff, 0xff, 0xff, 0xff, 0xff, 0xff],
    [0x00, 0x00, 0x00, 0x00, 0x00, 0x00, 0xff, 0xff, 0xff, 0xff, 0xff, 0xff],
    [0x00, 0x00, 0x00, 0x00, 0x00, 0x00, 0xff, 0xff, 0xff, 0xff, 0xff, 0xff],
    [0x00, 0x00, 0x00, 0x00, 0x00, 0x00, 0x00, 0xff, 0xff, 0xff, 0xff, 0x00],
    [0x00, 0x00, 0x00, 0x00, 0x00, 0x00, 0x00, 0x00, 0xff, 0xff, 0x00, 0x00],
    [0x00, 0x00, 0x00, 0x00, 0x00, 0x00, 0x00, 0x00, 0xff, 0xff, 0x00, 0x00],
    [0x00, 0x00, 0x00, 0x00, 0x00, 0x00, 0x00, 0x00, 0xff, 0xff, 0x00, 0x00],
    [0x00, 0x00, 0x00, 0x00, 0x00, 0x00, 0x00, 0xff, 0xff, 0xff, 0xff, 0x00],
    [0x00, 0x00, 0x00, 0x00, 0x00, 0x00, 0xff, 0xff, 0xff, 0xff, 0xff, 0xff],
    [0x00, 0x00, 0x00, 0x00, 0x00, 0x00, 0xff, 0xff, 0xff, 0xff, 0xff, 0xff],
    [0x00, 0x00, 0x00, 0x00, 0x00, 0x00, 0xff, 0xff, 0xff, 0xff, 0xff, 0xff],
    [0x00, 0x00, 0x00, 0x00, 0x00, 0x00, 0xff, 0xff, 0xff, 0xff, 0xff, 0xff]
]

transducerAnimationParticleToParticle2 = [
    [0x00, 0x00, 0x00, 0x00, 0x00, 0x00, 0xff, 0xff, 0xff, 0xff, 0xff, 0xff],
    [0x00, 0x00, 0x00, 0x00, 0x00, 0x00, 0xff, 0xff, 0xff, 0xff, 0xff, 0xff],
    [0x00, 0x00, 0x00, 0x00, 0x00, 0x00, 0xff, 0xff, 0xff, 0xff, 0xff, 0xff],
    [0x00, 0x00, 0x00, 0x00, 0x00, 0x00, 0xff, 0xff, 0xff, 0xff, 0xff, 0xff],
    [0x00, 0x00, 0x00, 0x00, 0x00, 0x00, 0xff, 0xff, 0xff, 0xff, 0xff, 0xff],
    [0x00, 0x00, 0x00, 0x00, 0x00, 0x00, 0xff, 0xff, 0xff, 0xff, 0xff, 0xff],
    [0x00, 0x00, 0x00, 0x00, 0x00, 0x00, 0xff, 0xff, 0xff, 0xff, 0xff, 0xff],
    [0x00, 0x00, 0x00, 0x00, 0x00, 0x00, 0xff, 0xff, 0xff, 0xff, 0xff, 0xff],
    [0x00, 0x00, 0x00, 0x00, 0x00, 0x00, 0xff, 0xff, 0xff, 0xff, 0xff, 0xff],
    [0x00, 0x00, 0x00, 0x00, 0x00, 0x00, 0xff, 0xff, 0xff, 0xff, 0xff, 0xff],
    [0x00, 0x00, 0x00, 0x00, 0x00, 0x00, 0xff, 0xff, 0xff, 0xff, 0xff, 0xff],
    [0x00, 0x00, 0x00, 0x00, 0x00, 0x00, 0xff, 0xff, 0xff, 0xff, 0xff, 0xff],
    [0x00, 0x00, 0x00, 0x00, 0x00, 0x00, 0xff, 0xff, 0xff, 0xff, 0xff, 0xff],
    [0x00, 0x00, 0x00, 0x00, 0x00, 0x00, 0xff, 0xff, 0xff, 0xff, 0xff, 0xff],
    [0x00, 0x00, 0x00, 0x00, 0x00, 0x00, 0xff, 0xff, 0xff, 0xff, 0xff, 0xff],
    [0x00, 0x00, 0x00, 0x00, 0x00, 0x00, 0xff, 0xff, 0xff, 0xff, 0xff, 0xff]
]
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

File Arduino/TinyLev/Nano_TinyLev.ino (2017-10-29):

#include <avr/sleep.h>
#include <avr/power.h>

#define N_PORTS 1
#define N_DIVS 24

#define WAIT_LOT(a) __asm__ __volatile__ ("nop"); __asm__ __volatile__ ("nop"); __asm__ __volatile__ ("nop");  __asm__ __volatile__ ("nop"); __asm__ __volatile__ ("nop");__asm__ __volatile__ ("nop"); __asm__ __volatile__ ("nop");__asm__ __volatile__ ("nop"); __asm__ __volatile__ ("nop");  __asm__ __volatile__ ("nop"); __asm__ __volatile__ ("nop");__asm__ __volatile__ ("nop");  __asm__ __volatile__ ("nop");  __asm__ __volatile__ ("nop")
#define WAIT_MID(a) __asm__ __volatile__ ("nop"); __asm__ __volatile__ ("nop"); __asm__ __volatile__ ("nop");  __asm__ __volatile__ ("nop"); __asm__ __volatile__ ("nop");__asm__ __volatile__ ("nop"); __asm__ __volatile__ ("nop");__asm__ __volatile__ ("nop"); __asm__ __volatile__ ("nop"); __asm__ __volatile__ ("nop"); __asm__ __volatile__ ("nop"); __asm__ __volatile__ ("nop"); __asm__ __volatile__ ("nop")
#define WAIT_LIT(a) __asm__ __volatile__ ("nop"); __asm__ __volatile__ ("nop"); __asm__ __volatile__ ("nop");  __asm__ __volatile__ ("nop"); __asm__ __volatile__ ("nop");  __asm__ __volatile__ ("nop");  __asm__ __volatile__ ("nop");  __asm__ __volatile__ ("nop");  __asm__ __volatile__ ("nop")


#define OUTPUT_WAVE(pointer, d)  PORTC = pointer[d*N_PORTS + 0]

#define N_BUTTONS 6
//half a second
#define STEP_SIZE 1
#define BUTTON_SENS 2500 
#define N_FRAMES 24

static byte frame = 0;
static byte animation[N_FRAMES][N_DIVS] = 
{{0x5,0x5,0x5,0x5,0x5,0x5,0x5,0x5,0x5,0x5,0x5,0x5,0xa,0xa,0xa,0xa,0xa,0xa,0xa,0xa,0xa,0xa,0xa,0xa},
{0x9,0x5,0x5,0x5,0x5,0x5,0x5,0x5,0x5,0x5,0x5,0x5,0x6,0xa,0xa,0xa,0xa,0xa,0xa,0xa,0xa,0xa,0xa,0xa},
{0x9,0x9,0x5,0x5,0x5,0x5,0x5,0x5,0x5,0x5,0x5,0x5,0x6,0x6,0xa,0xa,0xa,0xa,0xa,0xa,0xa,0xa,0xa,0xa},
{0x9,0x9,0x9,0x5,0x5,0x5,0x5,0x5,0x5,0x5,0x5,0x5,0x6,0x6,0x6,0xa,0xa,0xa,0xa,0xa,0xa,0xa,0xa,0xa},
{0x9,0x9,0x9,0x9,0x5,0x5,0x5,0x5,0x5,0x5,0x5,0x5,0x6,0x6,0x6,0x6,0xa,0xa,0xa,0xa,0xa,0xa,0xa,0xa},
{0x9,0x9,0x9,0x9,0x9,0x5,0x5,0x5,0x5,0x5,0x5,0x5,0x6,0x6,0x6,0x6,0x6,0xa,0xa,0xa,0xa,0xa,0xa,0xa},
{0x9,0x9,0x9,0x9,0x9,0x9,0x5,0x5,0x5,0x5,0x5,0x5,0x6,0x6,0x6,0x6,0x6,0x6,0xa,0xa,0xa,0xa,0xa,0xa},
{0x9,0x9,0x9,0x9,0x9,0x9,0x9,0x5,0x5,0x5,0x5,0x5,0x6,0x6,0x6,0x6,0x6,0x6,0x6,0xa,0xa,0xa,0xa,0xa},
{0x9,0x9,0x9,0x9,0x9,0x9,0x9,0x9,0x5,0x5,0x5,0x5,0x6,0x6,0x6,0x6,0x6,0x6,0x6,0x6,0xa,0xa,0xa,0xa},
{0x9,0x9,0x9,0x9,0x9,0x9,0x9,0x9,0x9,0x5,0x5,0x5,0x6,0x6,0x6,0x6,0x6,0x6,0x6,0x6,0x6,0xa,0xa,0xa},
{0x9,0x9,0x9,0x9,0x9,0x9,0x9,0x9,0x9,0x9,0x5,0x5,0x6,0x6,0x6,0x6,0x6,0x6,0x6,0x6,0x6,0x6,0xa,0xa},
{0x9,0x9,0x9,0x9,0x9,0x9,0x9,0x9,0x9,0x9,0x9,0x5,0x6,0x6,0x6,0x6,0x6,0x6,0x6,0x6,0x6,0x6,0x6,0xa},
{0x9,0x9,0x9,0x9,0x9,0x9,0x9,0x9,0x9,0x9,0x9,0x9,0x6,0x6,0x6,0x6,0x6,0x6,0x6,0x6,0x6,0x6,0x6,0x6},
{0x5,0x9,0x9,0x9,0x9,0x9,0x9,0x9,0x9,0x9,0x9,0x9,0xa,0x6,0x6,0x6,0x6,0x6,0x6,0x6,0x6,0x6,0x6,0x6},
{0x5,0x5,0x9,0x9,0x9,0x9,0x9,0x9,0x9,0x9,0x9,0x9,0xa,0xa,0x6,0x6,0x6,0x6,0x6,0x6,0x6,0x6,0x6,0x6},
{0x5,0x5,0x5,0x9,0x9,0x9,0x9,0x9,0x9,0x9,0x9,0x9,0xa,0xa,0xa,0x6,0x6,0x6,0x6,0x6,0x6,0x6,0x6,0x6},
{0x5,0x5,0x5,0x5,0x9,0x9,0x9,0x9,0x9,0x9,0x9,0x9,0xa,0xa,0xa,0xa,0x6,0x6,0x6,0x6,0x6,0x6,0x6,0x6},
{0x5,0x5,0x5,0x5,0x5,0x9,0x9,0x9,0x9,0x9,0x9,0x9,0xa,0xa,0xa,0xa,0xa,0x6,0x6,0x6,0x6,0x6,0x6,0x6},
{0x5,0x5,0x5,0x5,0x5,0x5,0x9,0x9,0x9,0x9,0x9,0x9,0xa,0xa,0xa,0xa,0xa,0xa,0x6,0x6,0x6,0x6,0x6,0x6},
{0x5,0x5,0x5,0x5,0x5,0x5,0x5,0x9,0x9,0x9,0x9,0x9,0xa,0xa,0xa,0xa,0xa,0xa,0xa,0x6,0x6,0x6,0x6,0x6},
{0x5,0x5,0x5,0x5,0x5,0x5,0x5,0x5,0x9,0x9,0x9,0x9,0xa,0xa,0xa,0xa,0xa,0xa,0xa,0xa,0x6,0x6,0x6,0x6},
{0x5,0x5,0x5,0x5,0x5,0x5,0x5,0x5,0x5,0x9,0x9,0x9,0xa,0xa,0xa,0xa,0xa,0xa,0xa,0xa,0xa,0x6,0x6,0x6},
{0x5,0x5,0x5,0x5,0x5,0x5,0x5,0x5,0x5,0x5,0x9,0x9,0xa,0xa,0xa,0xa,0xa,0xa,0xa,0xa,0xa,0xa,0x6,0x6},
{0x5,0x5,0x5,0x5,0x5,0x5,0x5,0x5,0x5,0x5,0x5,0x9,0xa,0xa,0xa,0xa,0xa,0xa,0xa,0xa,0xa,0xa,0xa,0x6}};


void setup()
{

/*
 for (int i = 0; i < (N_PORTS*N_DIVS); ++i){
    animation[frame][i] =  0;
  }

  for (int i = 0; i < (N_PORTS*N_DIVS/2); ++i){
     animation[frame][i] = 0b11111111;
  }
  
  for(int i = 0; i < N_DIVS; ++i){
    if (i % 2 == 0){
      animation[frame][i * N_PORTS] |= 0b00000001;
    }else{
      animation[frame][i * N_PORTS] &= 0b11111110;
    }
  }
*/
   DDRC = 0b00001111; //A0 to A3 are the signal outputs
   PORTC = 0b00000000; 
   
   pinMode(10, OUTPUT); //pin 10 (B2) will generate a 40kHz signal to sync 
   pinMode(11, INPUT_PULLUP); //pin 11 (B3) is the sync in
   //please connect pin 10 to pin 11

   for (int i = 2; i < 8; ++i){ //pin 2 to 7 (D2 to D7) are inputs for the buttons
    pinMode(i, INPUT_PULLUP); 
   }

  // generate a sync signal of 40khz in pin 10
  noInterrupts();           // disable all interrupts
  TCCR1A = bit (WGM10) | bit (WGM11) | bit (COM1B1); // fast PWM, clear OC1B on compare
  TCCR1B = bit (WGM12) | bit (WGM13) | bit (CS10);   // fast PWM, no prescaler
  OCR1A =  (F_CPU / 40000L) - 1;
  OCR1B = (F_CPU / 40000L) / 2;
  interrupts();             // enable all interrupts

  // disable everything that we do not need 
  ADCSRA = 0;  // ADC
  power_adc_disable ();
  power_spi_disable();
  power_twi_disable();
  power_timer0_disable();
  //power_usart0_disable();
  Serial.begin(115200);

 byte* emittingPointer = &animation[frame][0];
 byte buttonsPort = 0;

 bool anyButtonPressed;
 bool buttonPressed[N_BUTTONS];
 short buttonCounter = 0;

  LOOP:
    while(PINB & 0b00001000); //wait for pin 11 (B3) to go low 
    
    OUTPUT_WAVE(emittingPointer, 0); buttonsPort = PIND; WAIT_LIT();
    OUTPUT_WAVE(emittingPointer, 1); anyButtonPressed = (buttonsPort & 0b11111100) != 0b11111100; WAIT_MID();
    OUTPUT_WAVE(emittingPointer, 2); buttonPressed[0] = buttonsPort & 0b00000100; WAIT_MID();
    OUTPUT_WAVE(emittingPointer, 3); buttonPressed[1] = buttonsPort & 0b00001000; WAIT_MID();
    OUTPUT_WAVE(emittingPointer, 4); buttonPressed[2] = buttonsPort & 0b00010000; WAIT_MID();
    OUTPUT_WAVE(emittingPointer, 5); buttonPressed[3] = buttonsPort & 0b00100000; WAIT_MID();
    OUTPUT_WAVE(emittingPointer, 6); buttonPressed[4] = buttonsPort & 0b01000000; WAIT_MID();
    OUTPUT_WAVE(emittingPointer, 7); buttonPressed[5] = buttonsPort & 0b10000000; WAIT_MID();
    OUTPUT_WAVE(emittingPointer, 8); WAIT_LOT();
    OUTPUT_WAVE(emittingPointer, 9); WAIT_LOT();
    OUTPUT_WAVE(emittingPointer, 10); WAIT_LOT();
    OUTPUT_WAVE(emittingPointer, 11); WAIT_LOT();
    OUTPUT_WAVE(emittingPointer, 12); WAIT_LOT();
    OUTPUT_WAVE(emittingPointer, 13); WAIT_LOT();
    OUTPUT_WAVE(emittingPointer, 14); WAIT_LOT();
    OUTPUT_WAVE(emittingPointer, 15); WAIT_LOT();
    OUTPUT_WAVE(emittingPointer, 16); WAIT_LOT();
    OUTPUT_WAVE(emittingPointer, 17); WAIT_LOT();
    OUTPUT_WAVE(emittingPointer, 18); WAIT_LOT();
    OUTPUT_WAVE(emittingPointer, 19); WAIT_LOT();
    OUTPUT_WAVE(emittingPointer, 20); WAIT_LOT();
    OUTPUT_WAVE(emittingPointer, 21); WAIT_LOT();
    OUTPUT_WAVE(emittingPointer, 22); WAIT_LOT();
    OUTPUT_WAVE(emittingPointer, 23);
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

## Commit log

2017-10-29 Add tinylev code for arduino
2017-10-29 added test code for arduino
2017-10-29 added button code with test
2017-11-01 Fixed button using port value directly Fixed index for steady state and animation state, animation code generation Code cleanup
2017-11-23 Beaucoup changements : séquence de déplacement, possibilité de changer la vitesse de déplacement en changeant le nombre d'itérations
2017-11-23 Added 3d print files and electronic schematic
    [Base a imprimer.stl, Cube de pilier à imprimer 9x.stl, Nouveau pilier imrpimer 9x.stl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]
2017-11-25 Modification of name of pieces, added fritzzing file
    [Cube of the pilar for the support of L298N drivers.stl, Leviator schematic.fzz, Part 1 of the Leviator.stl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]
2018-02-20 Added Stl file of the Leviator 2 prototype and STL of the last pilar of the Leviator
    [Base Léviator 2.2.stl, Pilar of the Leviator n°3.stl, Pièce attache transducteur 2.1.stl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]
2018-05-12 Added new STL files and removed a few old ones
    [Cube of the pilar for the support of L298N drivers.stl, Leviator 2 Prototype part 1.stl, Leviator 2 prototype part 2.stl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]
2018-05-12 Added Gerber files of PCB prototypes for making a compact power supply for the transducers instead of using L298N drivers
    [copper_bottom.gbr, copper_top.gbr, drills.xln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]
2018-05-12 New images of the second Leviator prototype
